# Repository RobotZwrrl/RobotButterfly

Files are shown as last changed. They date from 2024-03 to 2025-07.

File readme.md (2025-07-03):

# Robot Butterfly

[Robot Butterfly](http://robotzwrrl.xyz/robot-butterfly/) invites you to experience nature's elegance alongside it, while interacting with the surrounding wilderness! [Available now as a kit](https://robotmissions.org/store/) to build yourself. 

For more information, check out: [robotzwrrl.xyz/robot-butterfly](http://robotzwrrl.xyz/robot-butterfly/). As well, see the [instructions](https://robotzwrrl.xyz/robot-butterfly/instructions/chapter01.php) to build your own!

Robot Butterfly's design files are released as open source hardware, provided under these unique terms: If you replicate it, please take a photo of it in nature and email it to me with the city and its nickname! ☺️

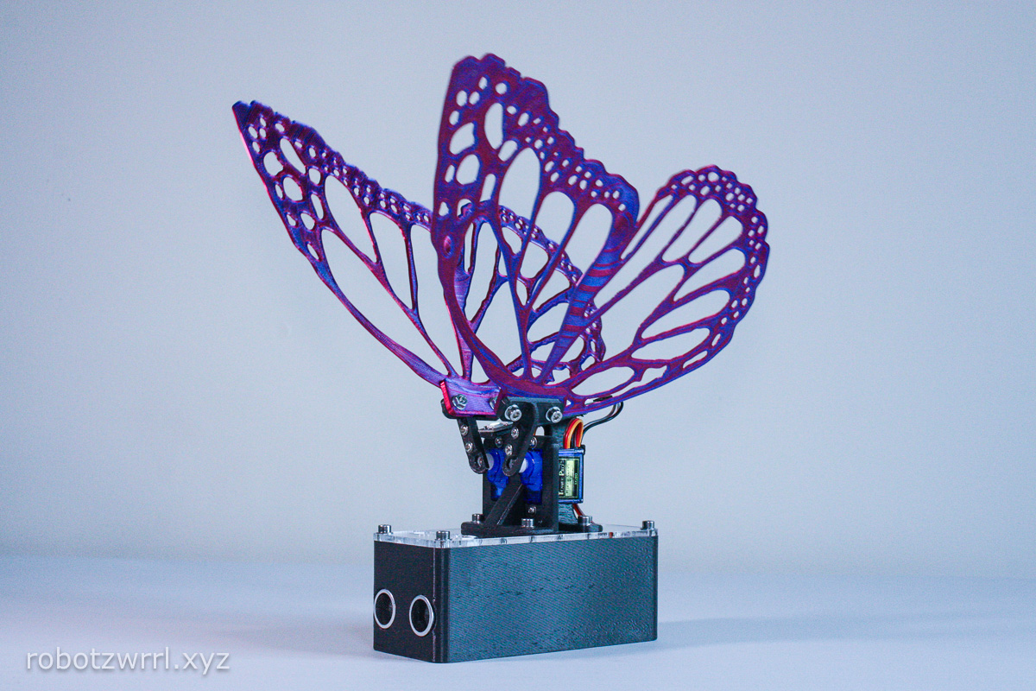
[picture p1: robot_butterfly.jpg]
Robot Butterfly


---

## Bug Fix 12-15-24

A 3D printable bugfix is available! The three pieces to print are:

- [Servo Horn Indent L](https://github.com/RobotGrrl/RobotButterfly/blob/main/3dprint/servo_horn_indent_L_v1.0.stl)
- [Servo Horn Indent R](https://github.com/RobotGrrl/RobotButterfly/blob/main/3dprint/servo_horn_indent_R_v1.0.stl)
- [Spacer Back](https://github.com/RobotGrrl/RobotButterfly/blob/main/3dprint/spacer_back_v1.1.stl)

The servo horn piece has been updated to work with the new horns that have an indent, rather than being flat in the previous version. The horn is placed on the side that has the arrow indicator. The fasteners go through holes #1 and #4. See photo below for reference.

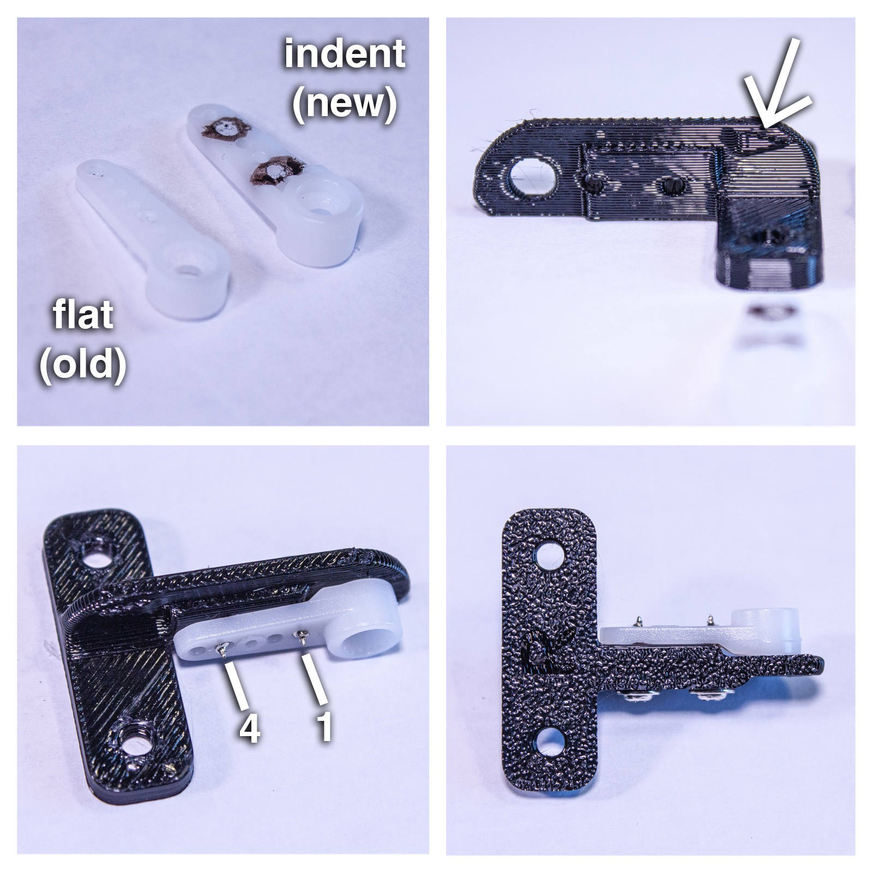
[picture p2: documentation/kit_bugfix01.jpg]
Bugfix 01


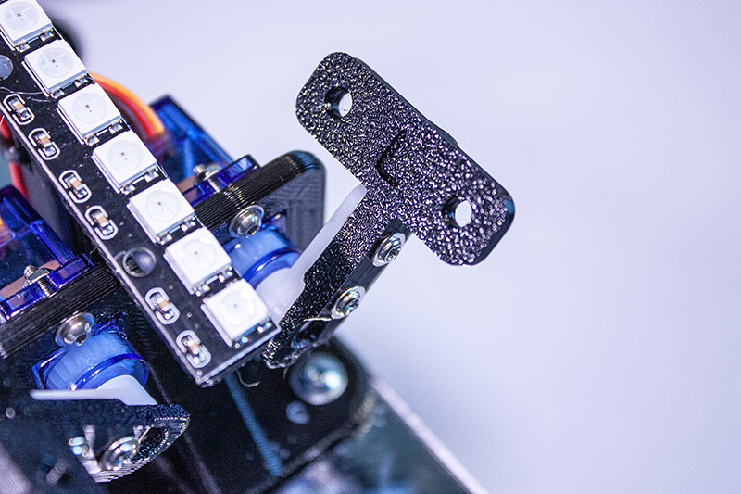
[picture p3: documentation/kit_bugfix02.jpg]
Bugfix 02


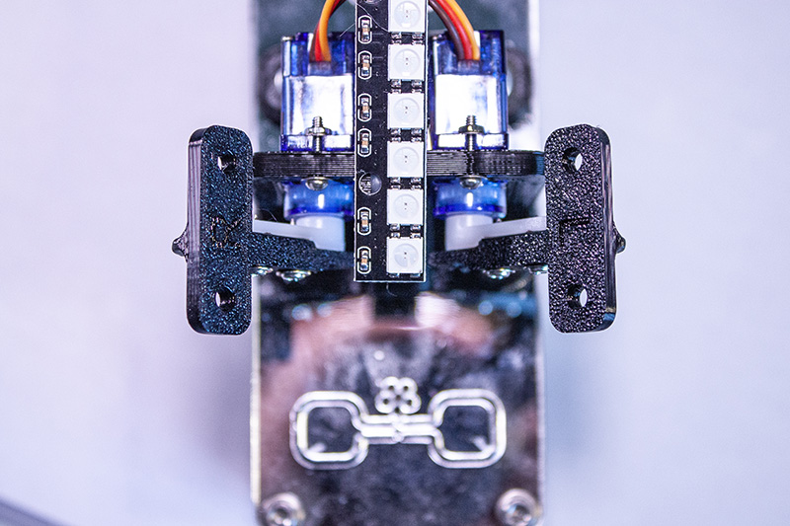
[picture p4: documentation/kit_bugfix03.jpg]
Bugfix 03


The spacer back piece has been updated to have clearance for the chamfer around the switch housing on the enclosure. This provides a cleaner fit and smoother lid installation process.

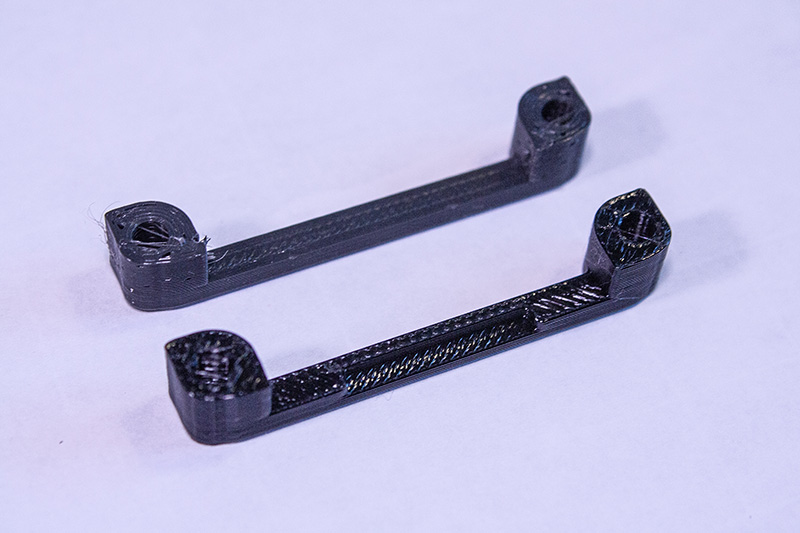
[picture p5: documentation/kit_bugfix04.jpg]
Bugfix 04


---

## Electronics

The Butterfly Chonky board connects with [Keystone](https://github.com/RobotGrrl/Keystone) and [Boostlet!](https://github.com/RobotGrrl/boostlet). Those two boards are also open source, and can be found in these repositories:

- https://github.com/RobotGrrl/boostlet
- https://github.com/RobotGrrl/Keystone

### What do the LEDs mean?

There are a few LEDs that are visible through the windows on the back of the enclosure.

On Chonky, there are two yellow 5 mm LEDs. On the left hand side, is D2. In the firmware, D2 is `LED_COMMS_PIN` (pin 5). On the right hand side, this is D1. In the firmware, D1 is `LED_HEARTBEAT_PIN` (pin 13).

LEDs from Keystone are also visible through the LED ports on the back side of the enclosure. As well, sometimes their brightness reflects in Chonky’s 5 mm LEDs. On the left hand side is power. The power LED is on all the time. On the right hand side are TX and RX. The TX and RX LEDs are activated whenever there is data on the serial port. This can be useful for a visual check, but it also just looks techno cool.

In the inaugural version, all the LEDs are yellow, which can sometimes make it tricky to visually differentiate between Chonky and Keystone's LEDs. This will be changed in a future production revision :)

---

## Manufacturing

| Piece | Layer height | Supports | Infill | Shells | Notes |
| --- | --- | --- | --- | --- | --- |
| enclosure_v1.0.stl | 0.25 mm DRAFT | Everwhere, Organic | 15% | 2 | \- |
| neopixel_bracket_v1.0.stl | 0.25 mm DRAFT | Everwhere, Organic | 15% | 3 | Prints standing up |
| battery_bracket_v1.0.stl  | 0.25 mm DRAFT | Supports to build platform | 15% | 2 | Hiya!' faces up, Top fill pattern: Octogram Spiral |
| lid_v1.1.stl | 0.25 mm DRAFT | None | 15% | 3 | Chamfer side down |
| servo_bracket_v1.0.stl | 0.25 mm DRAFT | None | 15% | 2 | Prints face down |
| servo_horn_indent_L_v1.0.stl | 0.20 mm QUALITY | None | 20% | 4 | \- |
| servo_horn_indent_R_v1.0.stl | 0.20 mm QUALITY | None | 20% | 4 | \- |
| cover_v1.0.stl | 0.25 mm DRAFT | None | 15% | 2 | Cool!' faces up |
| spacer_back_v1.1.stl | 0.25 mm DRAFT | None | 15% | 2 | Chamfer side down |
| spacer_front_v1.0.stl | 0.25 mm DRAFT | None | 15% | 2 | Chamfer side down |
| wing_L_v1.0.stl | 0.25 mm DRAFT | None | 15% | 3 | Top & bottom fill pattern: Archimedian Chords. Print 1st layer at a very slow speed. |
| wing_R_v1.0.stl | 0.25 mm DRAFT | None | 15% | 3 | Top & bottom fill pattern: Archimedian Chords. Print 1st layer at a very slow speed. |

---

## Firmware

**Firmware is in active development**

Download the [Robot Butterfly library](https://github.com/RobotZwrrl/RobotButterfly/tree/main/firmware/library/RobotButterfly) and install it into your Arduino library folder _(for example: ~/Documents/Arduino/libraries)_.

### Boards Manager

In the Arduino IDE boards manager (Tools > Board > Board Manager), search for **esp32**. Under **esp32 by Espressif Systems**, choose **2.0.4**, and install it.

### Library Dependencies

In the Arduino IDE library manager (Tools > Manage Libraries), please install the following libraries with the designated versions:

- [Streaming](https://github.com/janelia-arduino/Streaming) - v5.0.0
- [movingAvg](https://github.com/JChristensen/movingAvg) - v2.3.2
- [MPU6050](https://github.com/ElectronicCats/mpu6050) - v1.4.3
- [Adafruit Neopixel](https://github.com/adafruit/Adafruit_NeoPixel) - v.1.12.4
- [ESP32Servo](https://github.com/madhephaestus/ESP32Servo) - v3.0.6 
- [ServoEasing](https://github.com/ArminJo/ServoEasing) - v3.4.0
- [DHT](https://github.com/adafruit/DHT-sensor-library) - v1.4.6
- [Adafruit Unified Sensor](https://github.com/adafruit/Adafruit_Sensor) - v1.1.15 
- [HC-SR04](https://github.com/d03n3rfr1tz3/HC-SR04) - v1.1.3 

### Upload Code

Here's how to upload code to Robot Butterfly!

_Please see steps above to ensure all dependencies are installed properly_

1. Tools > Board > esp32 > Set board to **ESP32 Dev Module**

2. Tools > Set upload speed to **115200 baud** (at the bottom of the menu)

3. Tools > Set CPU speed to **80 MHz** (first setting after a divider in the menu)

4. Tools > Manage Libraries
There are library dependencies that will need to be downloaded, see list above

5. Open a Robot Butterfly example sketch

6. Plug in Robot Butterfly

7. Tools > Port > Select the port

8. Upload

9. Congrats! You have uploaded code to Robot Butterfly!

### Animations

For developers - here's how to make your own animation (servo and neopixel):

1. Add identifier to enum servoAnimName

`SERVO_ANIM_SOARING`

2. Add the run function prototype

`void runServoAnim_soaring(struct ServoAnimation *animation);`

3. Write the run function

`void runServoAnim_soaring(struct ServoAnimation *a) { ... }`

4. Write the init function

`void initServoAnim_soaring(struct ServoAnimation *a) { ... }`

5. Add the case to setServoAnim

`case SERVO_ANIM_SOARING: 
initServoAnim_soaring(a); 
break;`

6. Call the animation to run it!

`setServoAnim(&servo_animation_alert, SERVO_ANIM_SOARING, SERVO_ANIM_ALERT); 
startServoAnim(&servo_animation_alert);`

---

## Debugging

Please see [this page for debugging FAQ](https://robotzwrrl.xyz/robot-butterfly/instructions/debugging.php).

---

## License

Robot Butterfly (C) Copyright Erin RobotZwrrl, Robot Missions Inc.

05-30-24 v1.0

[RobotZwrrl.xyz/robot-butterfly](http://RobotZwrrl.xyz/robot-butterfly)

[RobotMissions.org](https://RobotMissions.org)

This hardware is released under:

CERN Open Hardware License Version 2.0 - Permissive (CERN-OHL-P)

[https://cern-ohl.web.cern.ch/](https://cern-ohl.web.cern.ch/)

The software is released under:

The MIT License

[https://opensource.org/license/mit](https://opensource.org/license/mit)

The documentation is released under:

CC-BY-SA-4.0

[https://creativecommons.org/licenses/by-sa/4.0/](https://creativecommons.org/licenses/by-sa/4.0/)

_Disclaimer: Distributed as is. No warranty is given. Not responsible or liable for any damage or harm that result from this product._

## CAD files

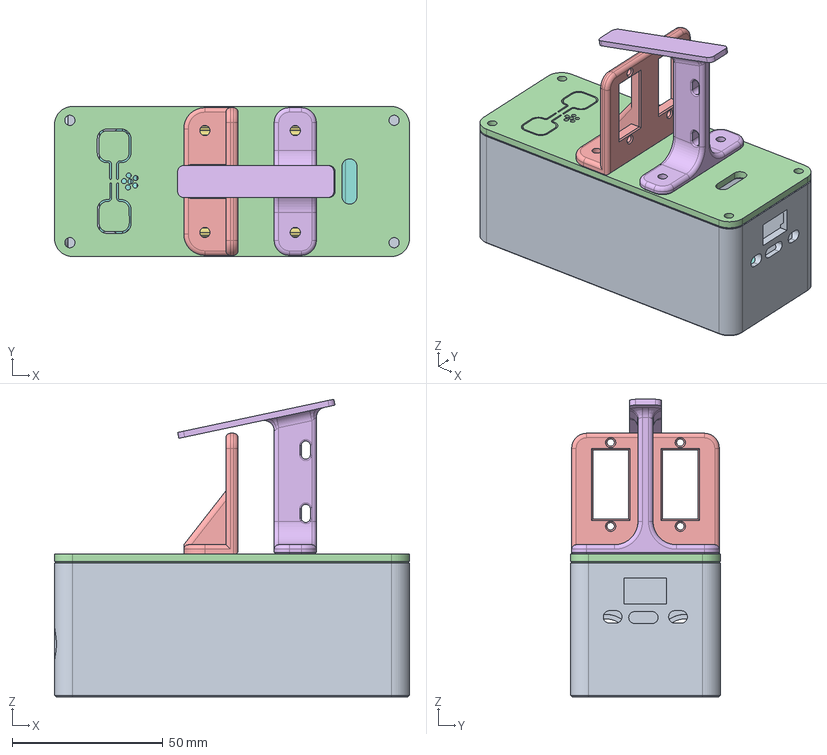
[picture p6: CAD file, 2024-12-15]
3dprint/assembly_v1.2.step
117.8 x 49.8 x 98.7 mm
enclosure_1
spacers
lid
servo bracket
neopixel bracket
cover
batt bracket

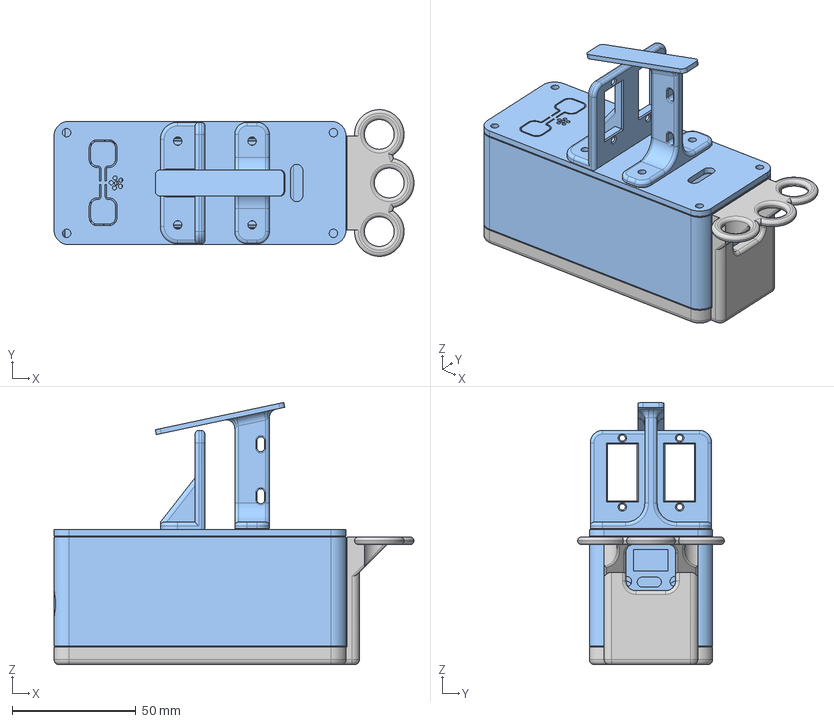
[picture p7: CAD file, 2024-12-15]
3dprint/extras/lanyard_attachment_v1.1.step
145.2 x 59.2 x 105.7 mm
enclosure_1
spacers
lid
servo bracket
neopixel bracket
cover
batt bracket

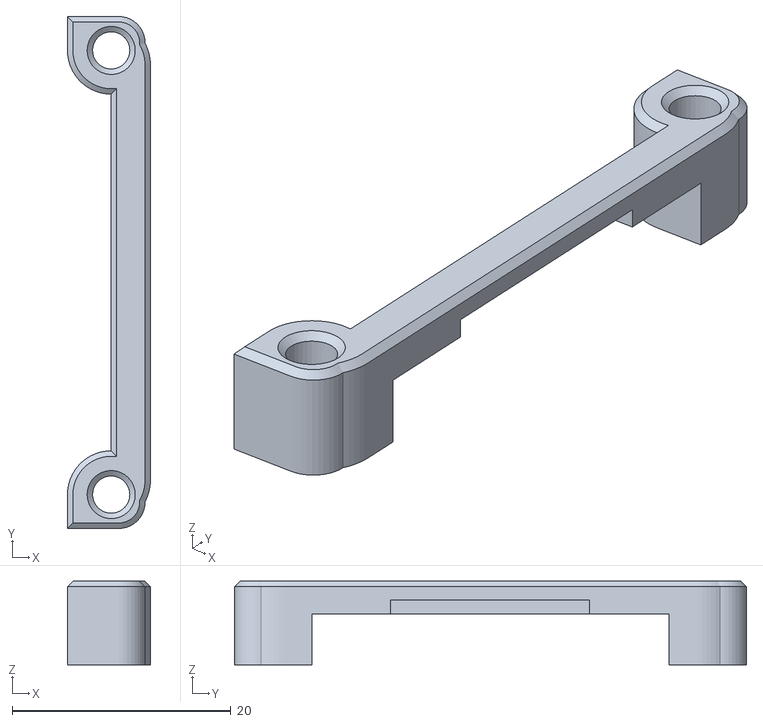
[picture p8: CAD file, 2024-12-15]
3dprint/spacer_back_v1.1.stl
7.60 x 46.8 x 7.65

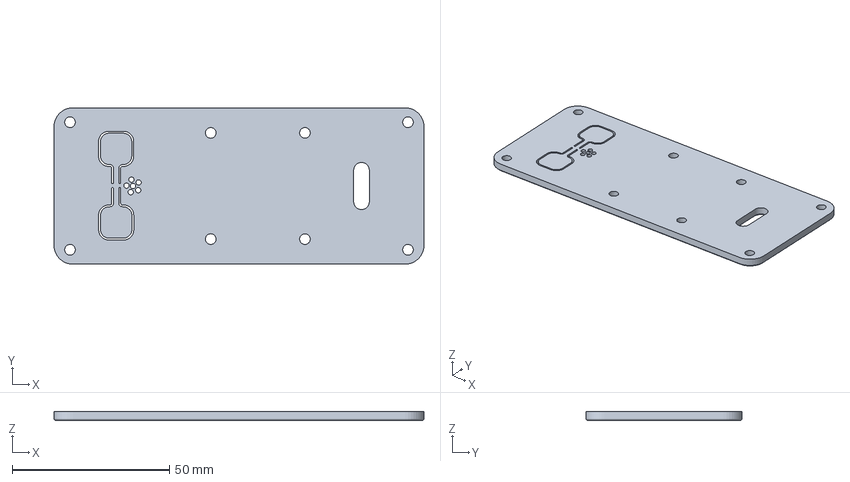
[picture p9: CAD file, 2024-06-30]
3dprint/z prusa mini/lid_v1.1.3mf
117.8 x 49.8 x 3.00 mm

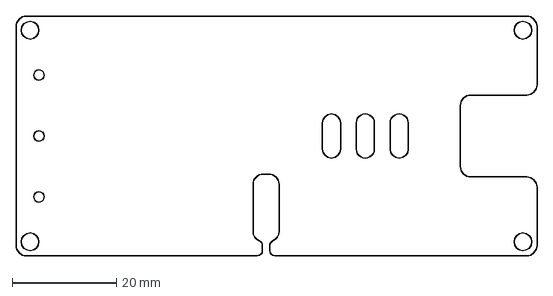
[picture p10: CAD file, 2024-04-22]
electronics/butterfly-chonky/outline-guide.dxf
100.0 x 46.0 mm

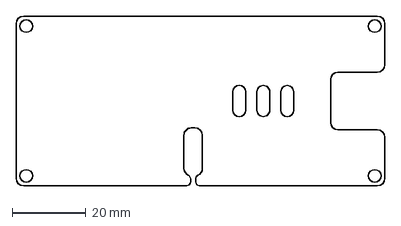
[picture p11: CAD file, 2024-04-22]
electronics/butterfly-chonky/outline.dxf
100.0 x 46.0 mm

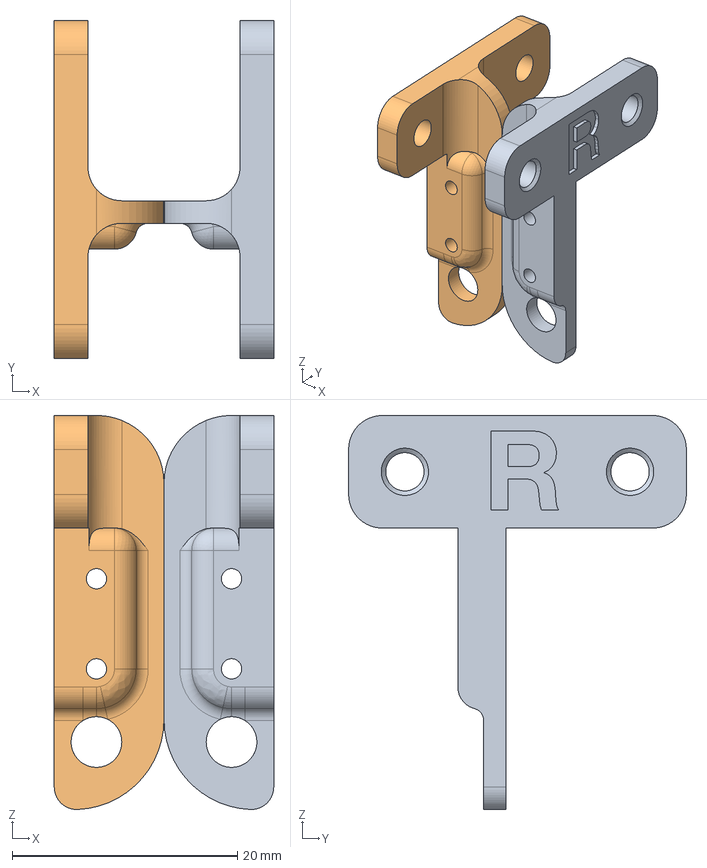
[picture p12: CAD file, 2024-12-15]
3dprint/servo_horn_flat_v1.0.step
19.5 x 30.0 x 35.0 mm
Component1(Mirror)

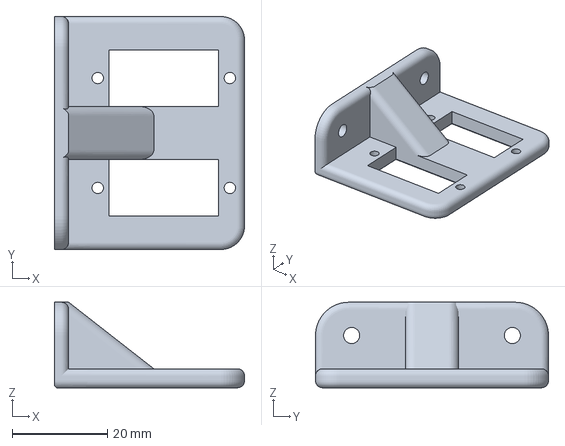
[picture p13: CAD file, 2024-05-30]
3dprint/z prusa mini/servo_bracket_v1.0.3mf
40.0 x 49.0 x 18.0 mm

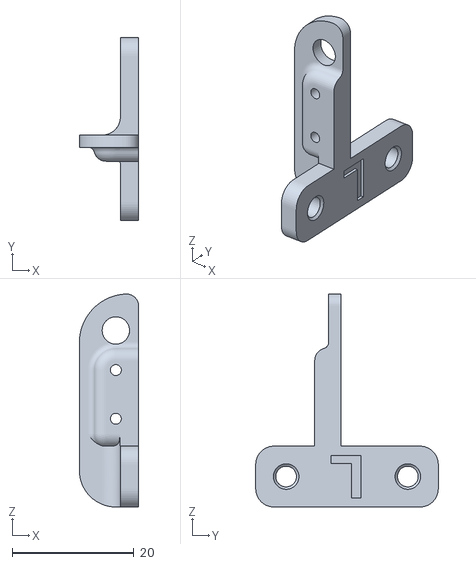
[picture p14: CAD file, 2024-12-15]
3dprint/servo_horn_flat_L_v1.0.stl
9.75 x 30.0 x 35.0

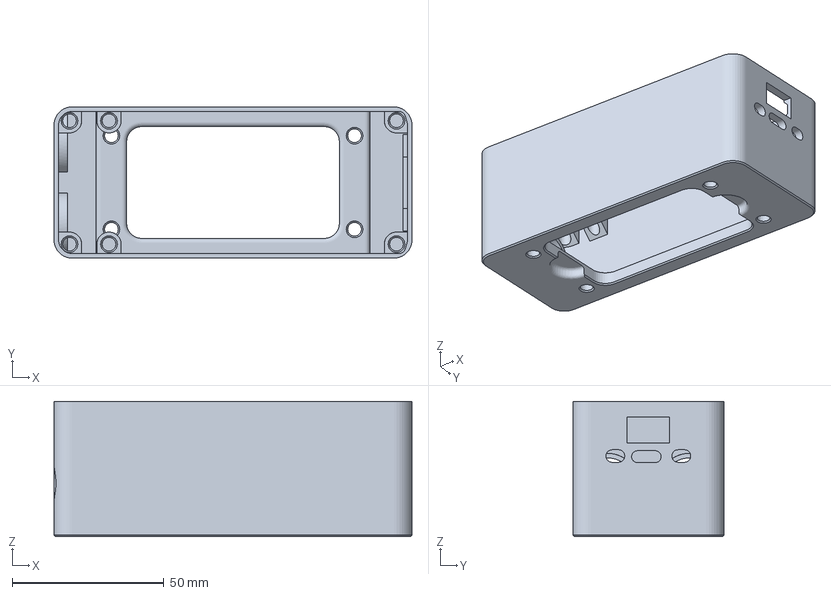
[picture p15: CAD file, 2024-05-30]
3dprint/z prusa mini/enclosure_v1.0.3mf
117.8 x 49.8 x 44.4 mm

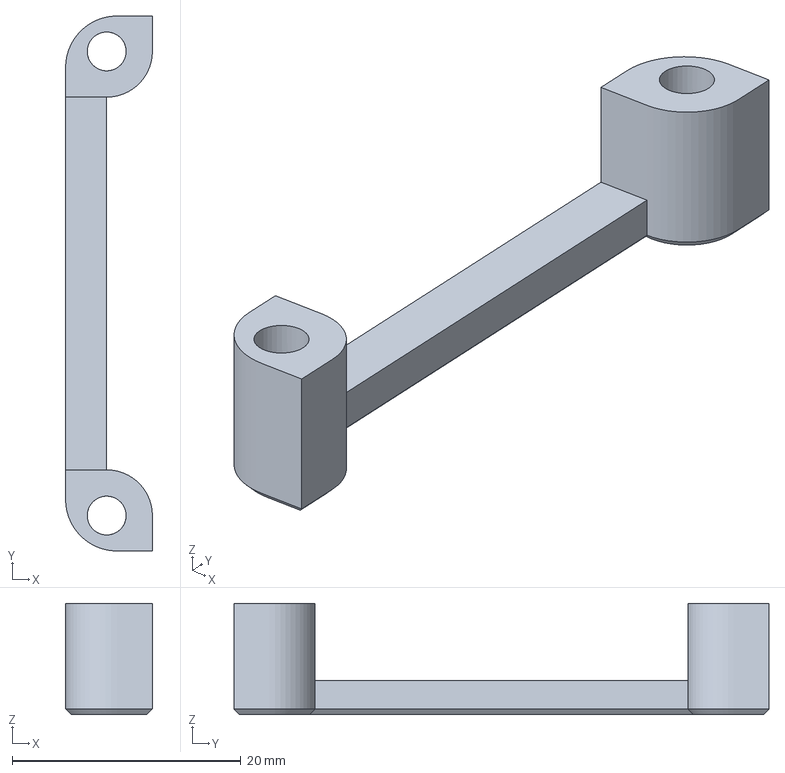
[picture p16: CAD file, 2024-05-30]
3dprint/z prusa mini/spacer_front_v1.0.3mf
7.60 x 46.8 x 9.75 mm

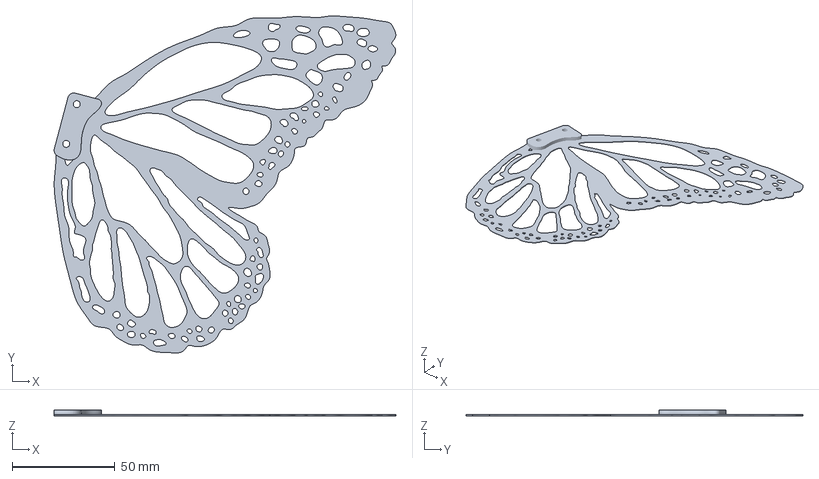
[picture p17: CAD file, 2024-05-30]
3dprint/z prusa mini/wing_L_v1.0.3mf
166.3 x 164.0 x 3.00 mm

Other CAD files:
3dprint/z prusa mini/spacer_back_v1.0.3mf
3dprint/servo_horn_indent_L_v1.0.stl
3dprint/z prusa mini/servo_horn_L_v1.0.3mf
3dprint/servo_horn_indent_v1.0.step
3dprint/servo_horn_indent_R_v1.0.stl
3dprint/servo_horn_flat_R_v1.0.stl
3dprint/archive/assembly_v1.0.step
3dprint/archive/assembly_v1.1.step
3dprint/archive/assembly_v1.1_no_colour.step
3dprint/archive/lid_v1.0.stl
3dprint/assembly_v1.1.step
3dprint/battery_bracket_v1.0.stl
3dprint/cover_v1.0.stl
3dprint/enclosure_v1.0.stl
3dprint/extras/lanyard_attachment_v1.0.step
3dprint/extras/lanyard_attachment_v1.1.stl
3dprint/lid_v1.0.dxf
3dprint/lid_v1.1.stl
3dprint/neopixel_bracket_v1.0.stl
3dprint/servo_bracket_v1.0.stl
3dprint/servo_horn_flat_v1.0.f3d
3dprint/servo_horn_indent_v1.0.f3d
3dprint/spacer_front_v1.0.stl
3dprint/wing_L_v1.0.stl
3dprint/wing_R_v1.0.stl
3dprint/z prusa mini/archive/lid_v1.0.3mf
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

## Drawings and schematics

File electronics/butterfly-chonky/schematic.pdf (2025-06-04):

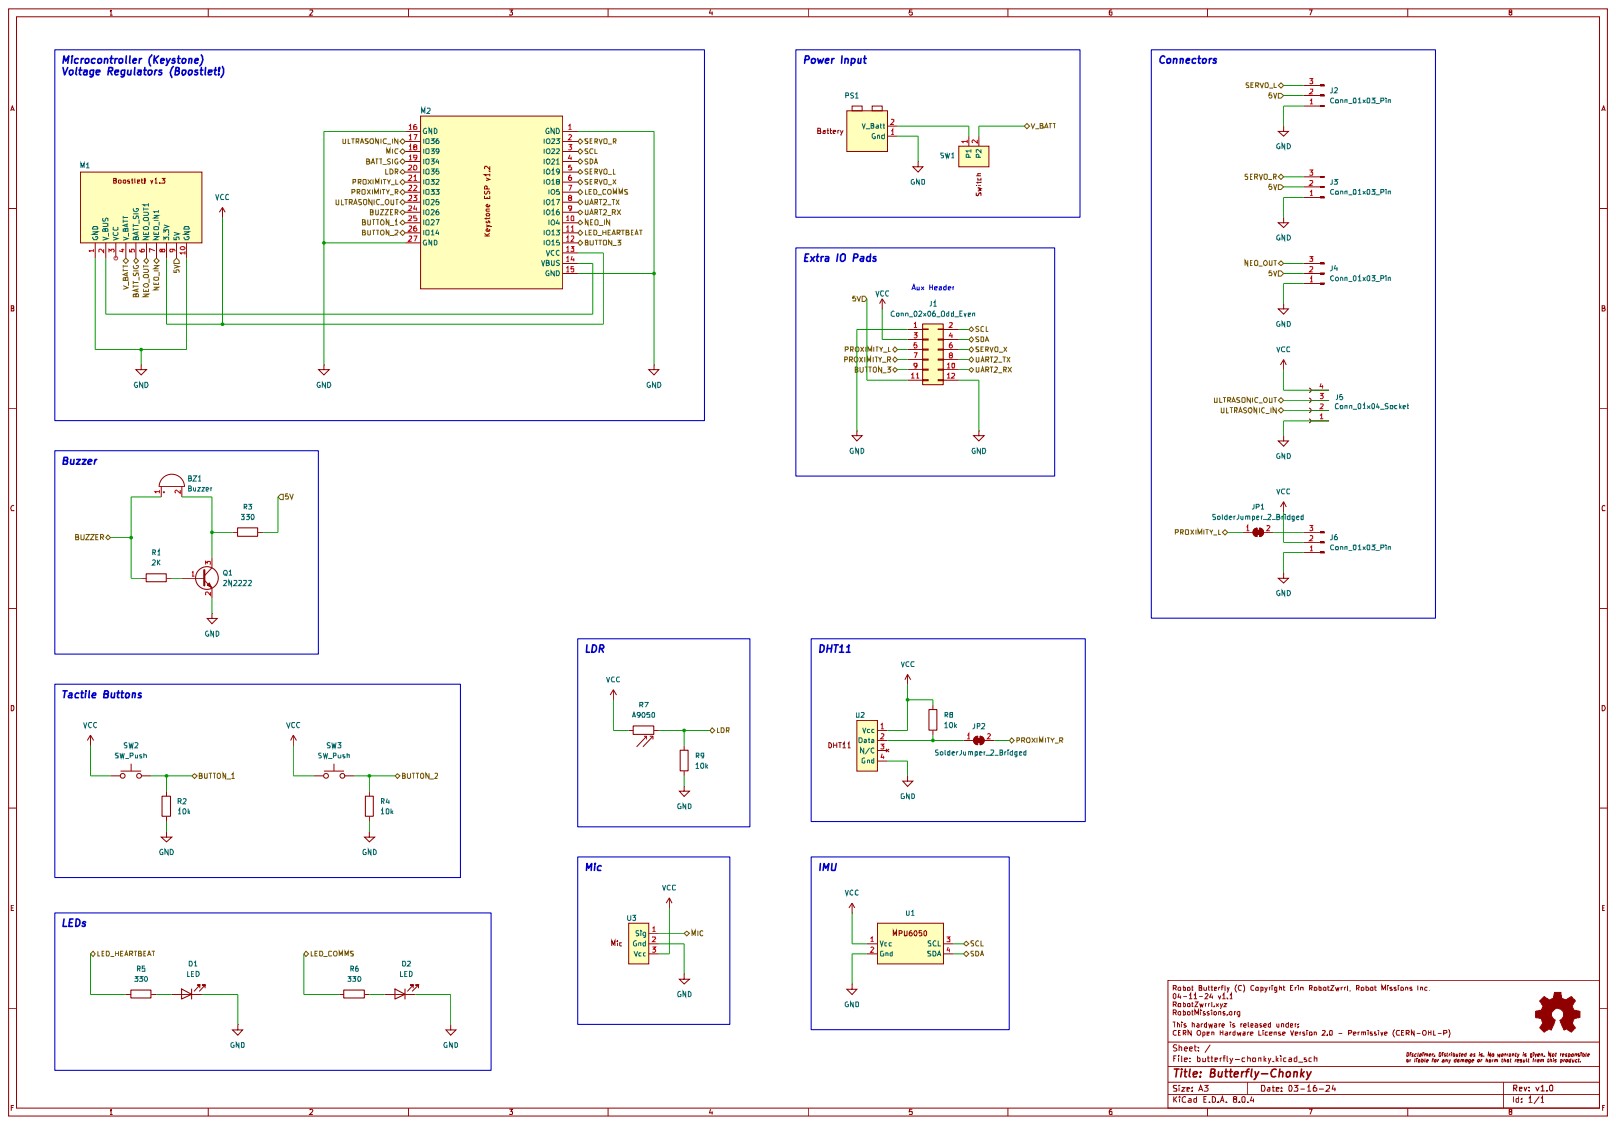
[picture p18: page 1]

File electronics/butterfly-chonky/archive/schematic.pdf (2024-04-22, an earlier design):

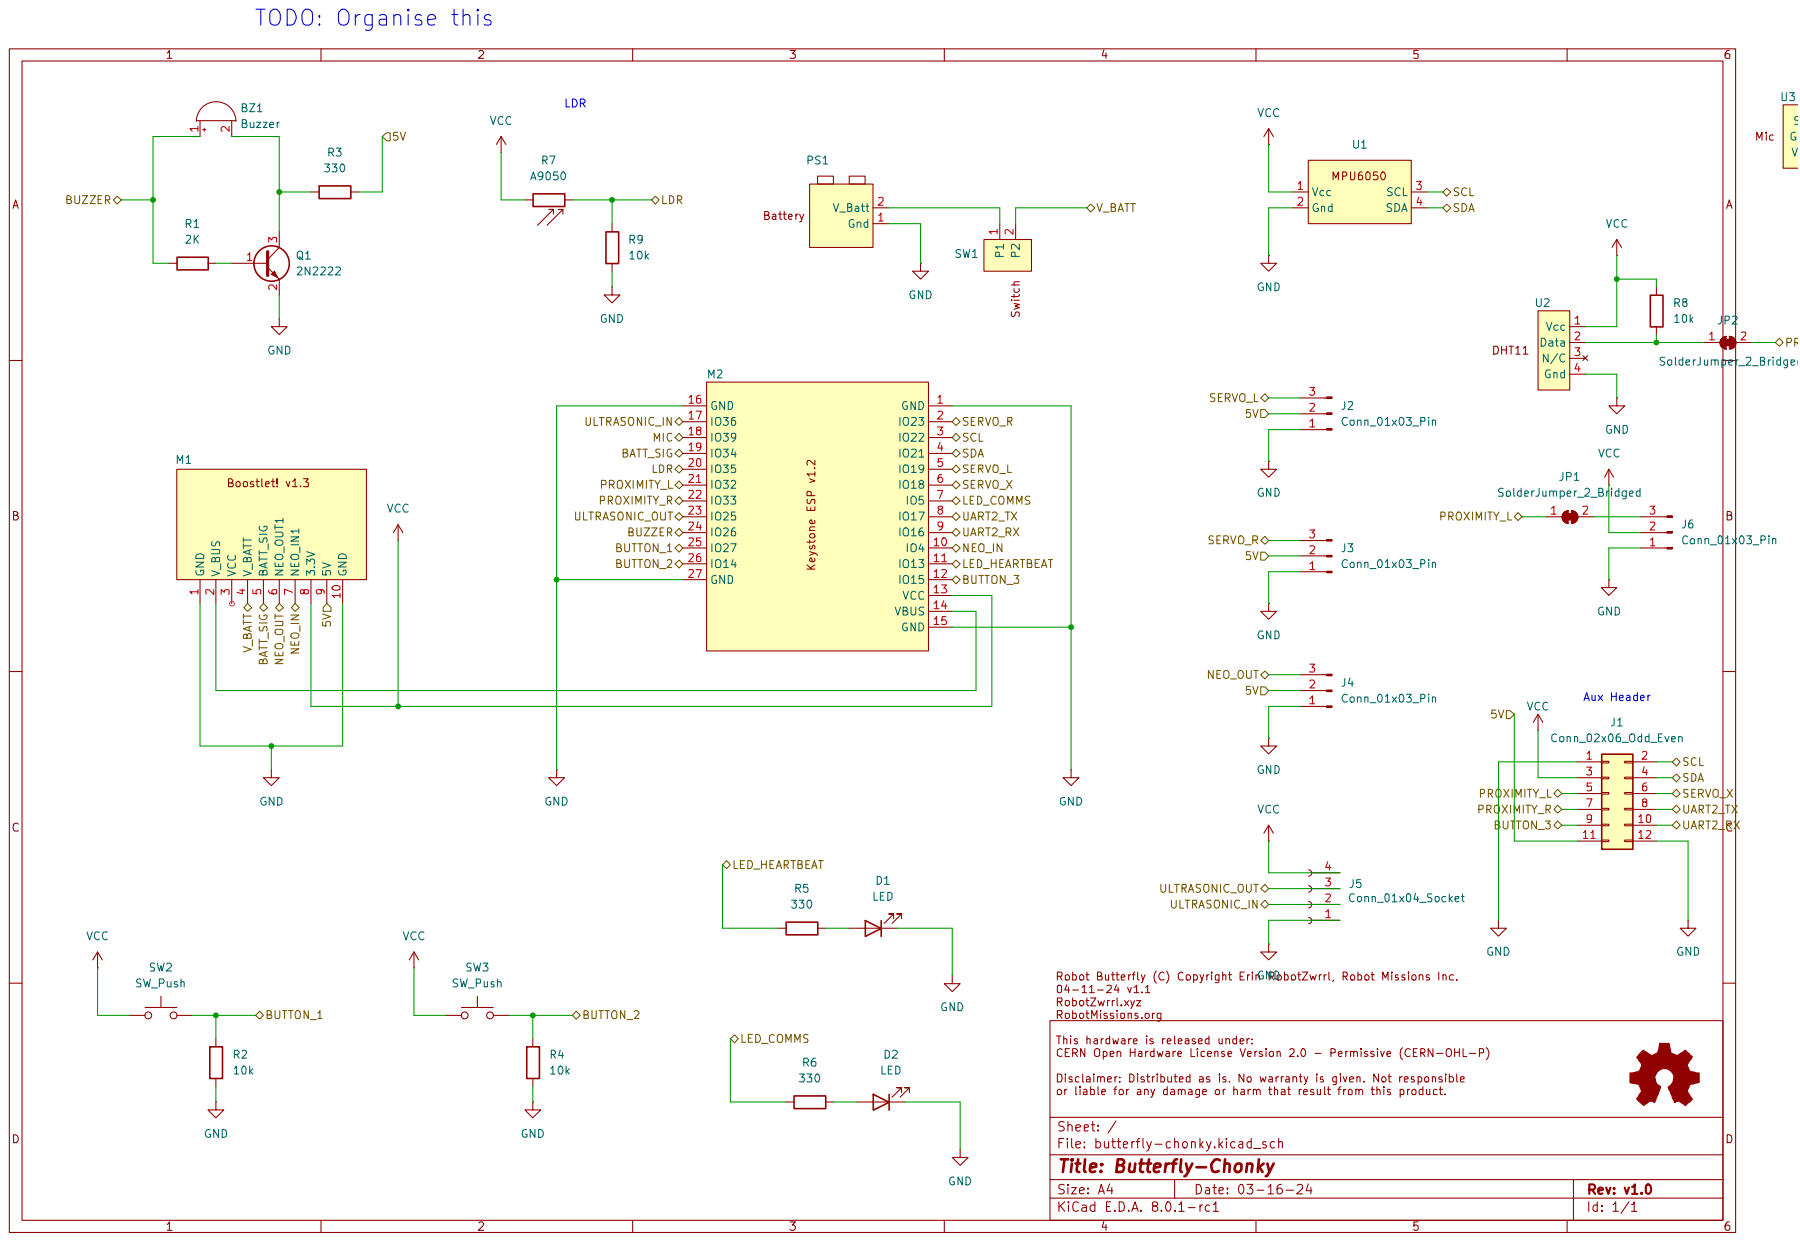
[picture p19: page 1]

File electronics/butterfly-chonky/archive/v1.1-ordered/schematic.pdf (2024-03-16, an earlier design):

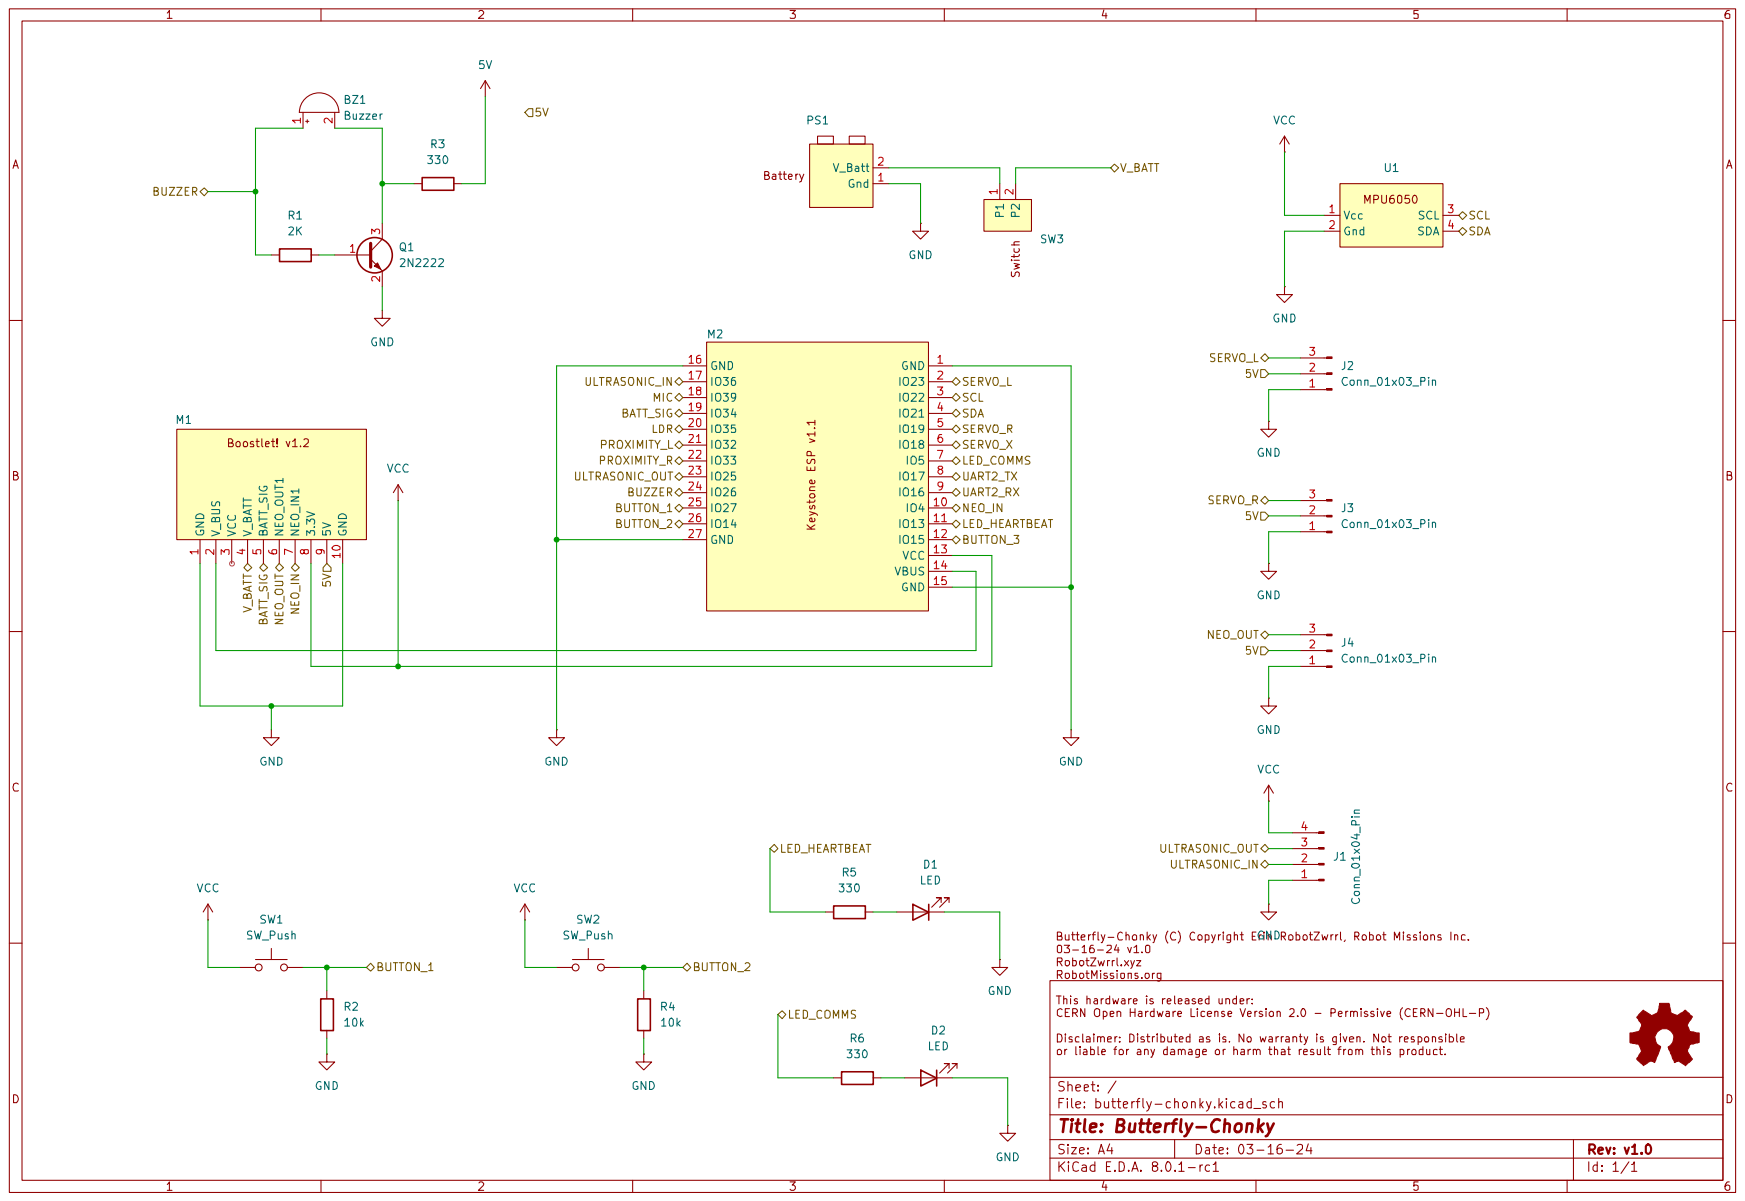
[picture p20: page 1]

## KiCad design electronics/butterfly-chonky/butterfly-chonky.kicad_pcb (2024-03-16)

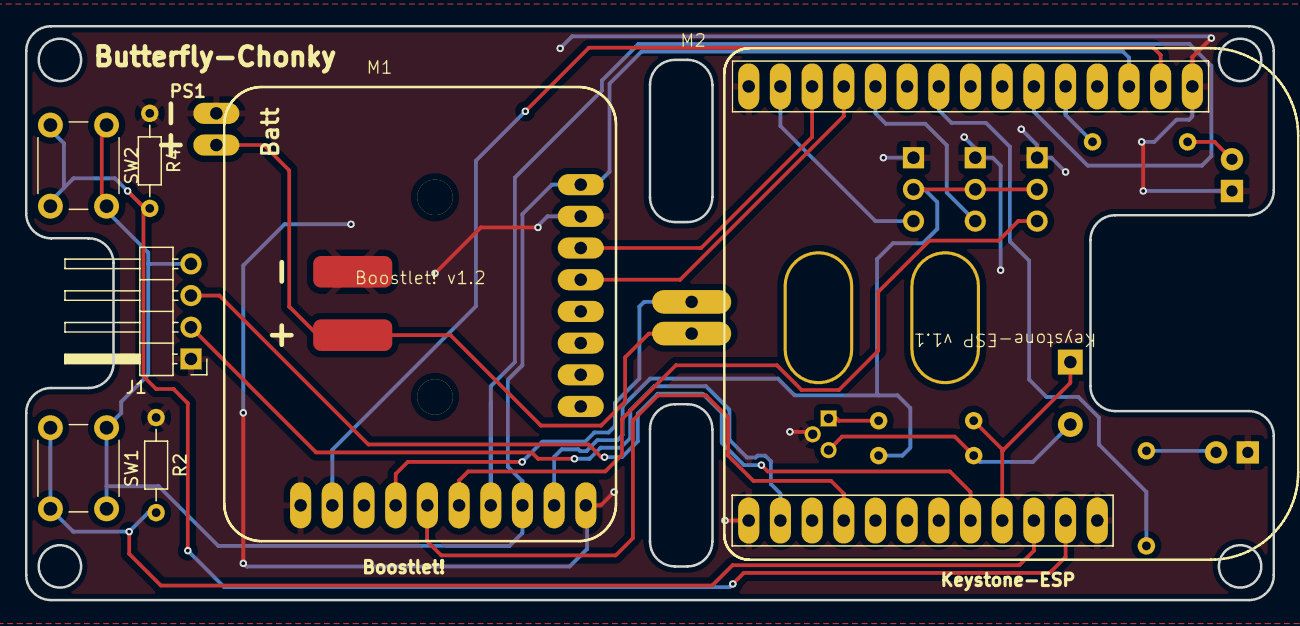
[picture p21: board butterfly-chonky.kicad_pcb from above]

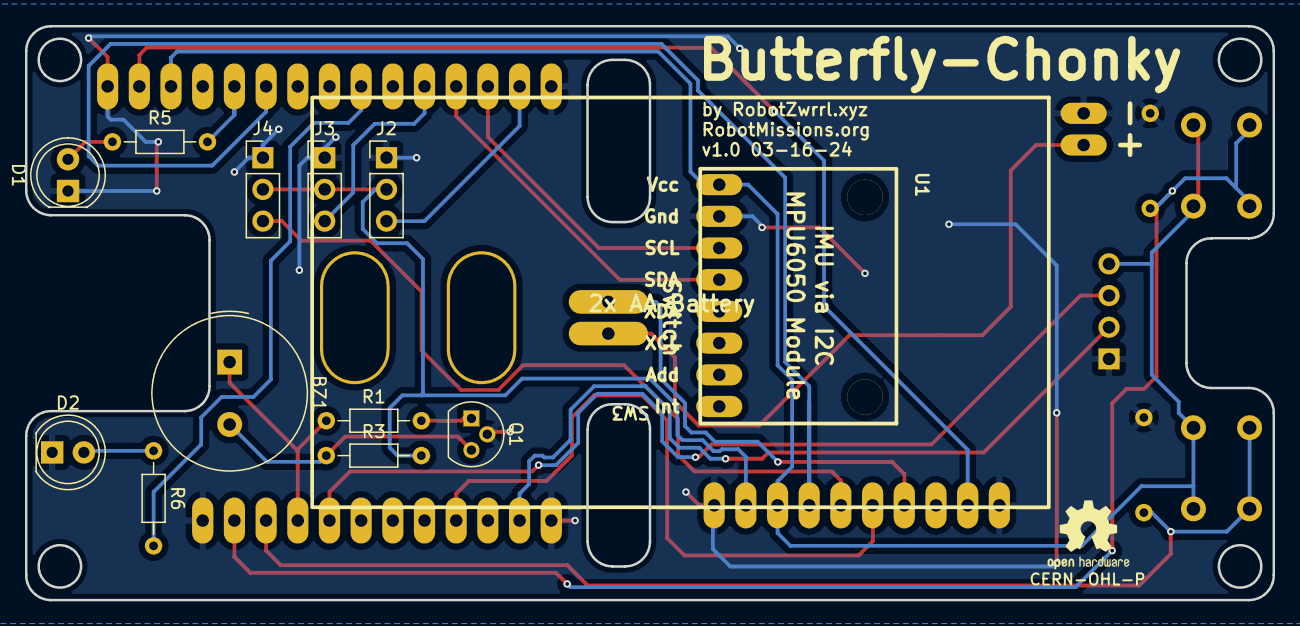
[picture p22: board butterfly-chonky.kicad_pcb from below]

Board: 2 copper layers, 100.0 x 46.0 mm, 21 parts (13 on the bottom side), 24 nets.

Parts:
BZ1: Buzzer; Buzzer_TDK_PS1240P02BT_D12.2mm_H6.5mm
D1, D2: LED; LED_D5.0mm_Clear
J1: Conn_01x04_Pin; PinHeader_1x04_P2.54mm_Horizontal
J2, J3, J4: Conn_01x03_Pin; PinHeader_1x03_P2.54mm_Vertical
M1: Boostlet_v1.2
M2: Keystone-ESP_v1.1
PS1: 2xAA_Battery_Module
Q1: 2N2222; TO-92
R1: 2K; R_Axial_DIN0204_L3.6mm_D1.6mm_P7.62mm_Horizontal
R2, R4: 10k; R_Axial_DIN0204_L3.6mm_D1.6mm_P7.62mm_Horizontal
R3, R5, R6: 330; R_Axial_DIN0204_L3.6mm_D1.6mm_P7.62mm_Horizontal
SW1, SW2: SW_Push; SW_PUSH_6mm_H5mm
SW3: Switch_Header
U1: MPU6050_Module

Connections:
5V: J2.2, J3.2, J4.2, M1.9 (5V), R3.2
/BATT_SIG: M1.5 (BATT_SIG), M2.19 (IO34)
/BUTTON_1: M2.25 (IO27), R2.2, SW1.2
/BUTTON_2: M2.26 (IO14), R4.2, SW2.2
/BUZZER: BZ1.1 (+), M2.24 (IO26), R1.1
/LED_COMMS: M2.7 (IO5), R6.2
/LED_HEARTBEAT: M2.11 (IO13), R5.2
/NEO_IN: M1.7 (NEO_IN1), M2.10 (IO4)
/NEO_OUT: J4.3, M1.6 (NEO_OUT1)
/SCL: M2.3 (IO22), U1.3 (SCL)
/SDA: M2.4 (IO21), U1.4 (SDA)
/SERVO_L: J2.3, M2.2 (IO23)
/SERVO_R: J3.3, M2.5 (IO19)
/ULTRASONIC_IN: J1.2, M2.17 (IO36)
/ULTRASONIC_OUT: J1.3, M2.23 (IO25)
/V_BATT: M1.4 (V_BATT), SW3.2
GND: D1.1 (K), D2.1 (K), J1.1, J2.1, J3.1, J4.1, M1.1 (GND), M1.10 (GND), M2.1 (GND), M2.15 (GND), M2.16 (GND), M2.27 (GND), PS1.1 (Gnd), Q1.2 (E), R2.1, R4.1, U1.2 (Gnd)
unnamed: BZ1.2 (-), Q1.3 (C), R3.1
unnamed: D1.2 (A), R5.1
unnamed: D2.2 (A), R6.1
unnamed: M1.2 (V_BUS), M2.14 (VBUS)
unnamed: PS1.2 (V_Batt), SW3.1
unnamed: Q1.1 (B), R1.2
VCC: J1.4, M1.8 (3.3V), M2.13 (VCC), SW1.1, SW2.1, U1.1 (Vcc)

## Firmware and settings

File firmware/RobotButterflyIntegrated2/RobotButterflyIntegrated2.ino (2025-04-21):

/*
 * Robot Butterfly Integrated 2
 * ----------------------------
 * Sandbox sketches together as one sketch
 * 
 * Board: ESP32 Dev Module
 * CPU speed: 80 MHz
 * Upload speed: 115200 baud
 * esp boards package: v 2.0.4 (<-- newer available)
 *
 * 21 Apr 2025 - Erin RobotZwrrl for Robot Missions Inc
 * http://robotzwrrl.xyz/robot-butterfly
 * http://robotmissions.org
 */

#include "Board.h"
#include "StateMachine_Params.h"
#include "Sound_Params.h"
#include "ServoAnim_Params.h"
#include "IMU_Params.h"
#include "Buttons_Params.h"
#include "Sensor_Params.h"
#include "Proximity_Params.h"
#include "NeoAnimations_Params.h"
#include "pitches.h"
#include <Streaming.h>
#include <ESP32Servo.h>      // 3.0.6 https://github.com/madhephaestus/ESP32Servo 
#include "ServoEasing.hpp"   // 3.4.0 https://github.com/ArminJo/ServoEasing
#include <movingAvg.h>   // 2.3.2 https://github.com/JChristensen/movingAvg
#include "DHT.h"         // 1.4.6 https://github.com/adafruit/DHT-sensor-library & 1.1.15 https://github.com/adafruit/Adafruit_Sensor 
#include <HCSR04.h>      // 1.1.3 https://github.com/d03n3rfr1tz3/HC-SR04 
#include "MPU6050.h"    // https://github.com/ElectronicCats/mpu6050/ 
#include <Adafruit_NeoPixel.h>


// ------------ states -----------
// this is where you can order the behaviours
enum StatesMachine {
  STATE1,
  STATE2,
  STATE3,
  STATE4,
  STATE5,
  STATE6,
  STATE7,
  STATE8
};

uint8_t CURRENT_STATE;
uint8_t PREV_STATE;
long last_state_change = 0;
long last_state_print = 0;

volatile bool enter_state = false;
volatile bool update_state = false;
volatile bool new_print = false;
volatile bool new_enter = false;
volatile bool new_update = false;
long t_transition = 0;
long t_enter = 0;
long t_delta = 0;

hw_timer_t *timer_state_cfg = NULL;

void IRAM_ATTR Timer_State_ISR() {
  enter_state = false;
  update_state = true;
  new_print = true;
  new_update = true;
}
// -------------------------------

// ----------- buzzer api ------------
void playSound(uint8_t id);
void soundDoneCallback(uint8_t id);
// -----------------------------------


// ------------ sound id -------------
enum soundID {
  SOUND_ALERT_STARTUP,
  SOUND_ALERT_ALERT,
  SOUND_ALERT_SLEEP,
  SOUND_ALERT_SNEEZE,
  SOUND_ALERT_MISSION_COMPLETE,
  SOUND_ALERT_MOONLIGHT_MODE,
  SOUND_ALERT_CHIRPY,
  SOUND_ALERT_WIFI_CONNECT,
  SOUND_ALERT_WIFI_DISCONNECT,
  SOUND_ALERT_MQTT_SEND,
  SOUND_ALERT_MQTT_RECEIVE,

  SOUND_SMELL_FLOWER,
  SOUND_SMELL_ROSE,
  SOUND_SMELL_WILDFLOWER,
  SOUND_SMELL_LAVENDER,
  SOUND_SMELL_DAISY,
  SOUND_SMELL_SUNFLOWER,

  SOUND_FLUTTER_MEMORY,
  SOUND_FLUTTER_JOY,
  SOUND_FLUTTER_CALM,
  SOUND_FLUTTER_SURPRISE,
  SOUND_FLUTTER_CONFUSED,
  SOUND_FLUTTER_SLEEPY,
  SOUND_FLUTTER_GRATEFUL
};
// -----------------------------------

// ----------- servo motors -----------
ServoEasing s1;
ServoEasing s2;

struct ServoMotor {
  ServoEasing motor;
  uint16_t home_pos;
  uint16_t up_pos;
  uint16_t down_pos;
  uint16_t current_pos;
  uint16_t target_pos;
  bool active;
  bool calibrated;
  String name;
};

enum ServoModeInit {
  SERVO_MODE_INIT_BOTH,
  SERVO_MODE_INIT_LEFT,
  SERVO_MODE_INIT_RIGHT
};

struct ServoMotor wing_left;
struct ServoMotor wing_right;

bool initialised_servos = false;
// -----------------------------------


// ----------- servo animation -----------
enum servoAnimName {
  SERVO_ANIM_NONE,
  SERVO_ANIM_GENTLE,
  SERVO_ANIM_SWAY,
  SERVO_ANIM_SOARING,
  SERVO_ANIM_TOUCHGRASS,
  SERVO_ANIM_SWOOSH,
  SERVO_ANIM_PARTY,
  SERVO_ANIM_FLUTTER,
  SERVO_ANIM_RANGE,
  SERVO_ANIM_POSITION
};

enum servoAnimType {
  SERVO_ANIM_ALERT,
  SERVO_ANIM_HOME
};

enum servoAnimFlutterWings {
  SERVO_ANIM_FLUTTER_WINGS_BOTH_HOME,
  SERVO_ANIM_FLUTTER_WINGS_BOTH_UP,
  SERVO_ANIM_FLUTTER_WINGS_LEFT_HOME,
  SERVO_ANIM_FLUTTER_WINGS_LEFT_UP,
  SERVO_ANIM_FLUTTER_WINGS_RIGHT_HOME,
  SERVO_ANIM_FLUTTER_WINGS_RIGHT_UP
};

enum servoAnimFlutterPos {
  SERVO_ANIM_FLUTTER_POS_NONE,
  SERVO_ANIM_FLUTTER_POS_HOME,
  SERVO_ANIM_FLUTTER_POS_UP,
  SERVO_ANIM_FLUTTER_POS_DOWN
};

enum servoAnimRangeSpan {
  SERVO_ANIM_RANGE_DOWN_UP,
  SERVO_ANIM_RANGE_HOME_UP,
  SERVO_ANIM_RANGE_ALT_HOME_UP
};

enum servoAnimPosition {
  SERVO_ANIM_POSITION_DOWN,
  SERVO_ANIM_POSITION_HOME,
  SERVO_ANIM_POSITION_UP
};

void runServoAnim_none(struct ServoAnimation *animation);
void runServoAnim_gentle(struct ServoAnimation *animation);
void runServoAnim_sway(struct ServoAnimation *animation);
void runServoAnim_soaring(struct ServoAnimation *animation);
void runServoAnim_touchgrass(struct ServoAnimation *animation);
void runServoAnim_swoosh(struct ServoAnimation *animation);
void runServoAnim_party(struct ServoAnimation *animation);
void runServoAnim_flutter(struct ServoAnimation *animation);
void runServoAnim_range(struct ServoAnimation *animation);
void runServoAnim_position(struct ServoAnimation *animation);
typedef void (*ServoAnimationFunction)(ServoAnimation*); // function pointer type that accepts a ServoAnimation pointer

struct ServoAnimation {
  uint8_t id;
  bool active;
  uint8_t type;
  uint8_t velocity;   // degrees per second

  uint8_t num_frames;
  uint16_t frame_delay;
  int frame_index;
  long last_frame;
  
  int num_repeats;
  uint16_t repeat_count;
  uint16_t repeat_delay;
  long last_repeat;

  long duration;
  long start_time;

  bool dir;
  int helper1;
  int helper2;
  int helper3;

  ServoAnimationFunction function;  // function pointer
};

ServoAnimation servo_animation_home;
ServoAnimation servo_animation_alert;
// -----------------------------------

// ------------ callbacks ------------
void proximityTriggerCallback(struct Proximity *p);
// ------------------------------------

// ----------- ultrasonic -------------
struct Proximity {
  bool initialised;
  long last_print;
  long last_trigger;
  uint8_t threshold;

  volatile bool update_raw;
  volatile uint8_t iteration_raw;
  volatile uint8_t reload_raw;
  uint16_t raw;
  uint16_t raw_prev;
  long last_raw;

  uint16_t val;
  uint16_t val_prev;
  movingAvg val_avg;

  Proximity() 
  : initialised(false), last_print(0), last_trigger(0), threshold(0),
    update_raw(false), iteration_raw(0), reload_raw(0), raw(0), raw_prev(0), last_raw(0),
    val_avg(PROXIMITY_MOVING_AVG_WINDOW, true)
{}

};

static struct Proximity ultrasonic;
// ------------------------------------

// ------------ callbacks ------------
void sensorLightChangeCallback(struct Sensor *s, bool trigger_dir);
void sensorLightAmbientChangeCallback(struct Sensor *s, int change);
void sensorSoundChangeCallback(struct Sensor *s, bool trigger_dir);
void sensorSoundAmbientChangeCallback(struct Sensor *s, int change);
void sensorTemperatureChangeCallback(struct Sensor *s, bool trigger_dir);
void sensorTemperatureAmbientChangeCallback(struct Sensor *s, int change);
void sensorHumidityChangeCallback(struct Sensor *s, bool trigger_dir);
void sensorHumidityAmbientChangeCallback(struct Sensor *s, int change);
// ------------------------------------

// -------------- vars ---------------
DHT dht(DHT11_PIN, DHT11);

uint16_t getSensor_Light(struct Sensor *s);
void updateSensor_Light(struct Sensor *s);
uint16_t getSensor_Battery(struct Sensor *s);
void updateSensor_Battery(struct Sensor *s);
uint16_t getSensor_Sound(struct Sensor *s);
void updateSensor_Sound(struct Sensor *s);
uint16_t getSensor_Temperature(struct Sensor *s);
void updateSensor_Temperature(struct Sensor *s);
uint16_t getSensor_Humidity(struct Sensor *s);
void updateSensor_Humidity(struct Sensor *s);
typedef uint16_t (*SensorDAQFunction)(Sensor*); // function pointer type that accepts a Sensor pointer
typedef void (*SensorUpdateFunction)(Sensor*); // function pointer type that accepts a Sensor pointer
// ------------------------------------

// --------------- sensor ----------------
hw_timer_t *timer_10Hz_config = NULL;

enum SensorIDs {
  SENSOR_ID_LIGHT,  
  SENSOR_ID_BATTERY,
  SENSOR_ID_SOUND,
  SENSOR_ID_TEMPERATURE,
  SENSOR_ID_HUMIDITY
};

struct Sensor {
  uint8_t id;
  String name;
  bool print;
  long print_frequency;
  long last_print;
  uint16_t trig_count;
  bool trigger_dir;
  long last_sensor_trigger;
  long last_ambient_trigger;

  // collected every 0.1 seconds
  volatile bool update_raw;
  volatile uint8_t iteration_raw;
  volatile uint8_t reload_raw;
  uint16_t raw;
  uint16_t raw_prev;
  long last_raw;

  // averaged over 1 seconds
  volatile bool update_val;
  volatile uint8_t iteration_val;
  volatile uint8_t reload_val;
  uint16_t val;
  uint16_t val_prev;
  long last_val;
  movingAvg val_avg;

  // averaged over 60 seconds
  volatile bool update_ambient;
  volatile uint16_t iteration_ambient;
  volatile uint16_t reload_ambient;
  uint16_t ambient;
  uint16_t ambient_prev;
  long last_ambient;
  movingAvg ambient_avg;
  int ambient_data[6];

  // ---
  SensorDAQFunction getRawData;        // function pointer
  SensorUpdateFunction updateSensor;   // function pointer

  // constructor
  Sensor()
  : id(0), name(""), print(true), print_frequency(0), last_print(0), trig_count(0), trigger_dir(false), last_sensor_trigger(0), last_ambient_trigger(0),
    update_raw(false), iteration_raw(0), reload_raw(0), raw(0), raw_prev(0), last_raw(0),
    update_val(false), iteration_val(0), reload_val(0), val(0), val_prev(0), last_val(0),
    val_avg(SENSOR_MOVING_AVG_VAL_WINDOW, true),
    update_ambient(false), iteration_ambient(0), reload_ambient(0), ambient(0), ambient_prev(0), last_ambient(0),
    ambient_avg(SENSOR_MOVING_AVG_AMBIENT_WINDOW, true),
    ambient_data(),
    getRawData(NULL), updateSensor(NULL)
  {}

};

static struct Sensor sensor_temperature;
static struct Sensor sensor_humidity;
static struct Sensor sensor_light;
static struct Sensor sensor_sound;
static struct Sensor sensor_battery;

static struct Sensor *all_sensors[NUM_SENSORS];

static bool dht_toggle = true;
static bool dht_processed = false;
static long last_dht_processed = 0;
// ------------------------------------

// ------------- sensor isr --------------
void IRAM_ATTR Timer_10Hz_ISR() { // every 0.1 seconds

  for(uint8_t i=0; i<NUM_SENSORS; i++) {
    struct Sensor *s = all_sensors[i];
    if(s == NULL) continue;

    // update raw every 0.1 second
    if(s->iteration_raw >= s->reload_raw-1) {
      s->update_raw = true; 
      s->iteration_raw = 0;
    } else {
      if(s->update_raw == false) {
        s->iteration_raw++;
      }
    }

    // update val every 1 second
    if(s->iteration_val >= s->reload_val-1) {
      s->update_val = true;
      s->iteration_val = 0;
    } else {
      if(s->update_val == false) {
        s->iteration_val++;
      }
    }

    // update ambient every 60 seconds
    if(s->iteration_ambient >= s->reload_ambient-1) {
      s->update_ambient = true;
      s->iteration_ambient = 0;
    } else {
      if(s->update_ambient == false) {
        s->iteration_ambient++;
      }
    }

  }


  // refresh ultrasonic every 0.5 seconds
  if(ultrasonic.iteration_raw >= ultrasonic.reload_raw-1) {
    ultrasonic.update_raw = true;
    ultrasonic.iteration_raw = 0;
  } else {
    if(ultrasonic.update_raw == false) {
      ultrasonic.iteration_raw++;
    }
  }


}
// ------------------------------------

// ----------- neoanim callbacks -----------
void callback_NeoAnimDone(struct NeoAnimation *a);
void callback_NeoAnimLoop(struct NeoAnimation *a);
// -----------------------------------


// ----------- neopixel colours -----------
// go with 400 kHz as 800 kHz would leave pixel colour ghosts
Adafruit_NeoPixel pixels(NEOPIXEL_COUNT, NEOPIXEL_PIN, NEO_GRB + NEO_KHZ400);

enum pastelIndex {
  NEO_RED,
  NEO_ORANGE,
  NEO_GOLDEN_YELLOW,
  NEO_CANARY_YELLOW,
  NEO_GREEN,
  NEO_SKY_BLUE,
  NEO_BLUE,
  NEO_CYAN,
  NEO_PURPLE,
  NEO_LAVENDER,
  NEO_PINK,
  NEO_MAGENTA,
  NEO_WARM_WHITE,
  NEO_WHITE,
  NEO_OFF
};

String pastelNames[NUM_PALETTE_COLOURS] = {
  "Red",
  "Orange",
  "Golden Yellow",
  "Canary Yellow",
  "Green",
  "Sky Blue",
  "Blue",
  "Cyan",
  "Purple",
  "Lavender",
  "Pink",
  "Magenta",
  "Warm White",
  "White",
  "Off"
};

// these are the colour settings when the 
// brightness is set to 20, which is visible
// during daylight outdoors
uint16_t pastelColours[NUM_PALETTE_COLOURS][3] = {
    {  100,  180,  250},   // red
    { 3500,  190,  250},   // orange
    { 6622,  190,  250},   // golden yellow
    { 9000,  190,  250},   // canary yellow
    {15545,  170,  250},   // green
    {32845,   50,  250},   // sky blue
    {43691,  120,  250},   // blue
    {27306,  120,  250},   // cyan
    {51613,  130,  250},   // purple
    {56613,   40,  250},   // lavendar
    {  359,   90,  250},   // pink
    {63535,  140,  250},   // magenta
    { 6561,  140,  250},   // warm white
    { 8192,   90,  250},   // white
    {    0,    0,    0},   // off
};

uint32_t colourPalette[NUM_PALETTE_COLOURS];
// -----------------------------------

// ------- neopixel animation --------
enum neoAnimName {
  NEO_ANIM_NONE,
  NEO_ANIM_POLKADOT,
  NEO_ANIM_SQUIGGLE,
  NEO_ANIM_RANGE,
  NEO_ANIM_FUNKY,
  NEO_ANIM_ZWOOP,
  NEO_ANIM_SPRINKLE,
  NEO_ANIM_RAINBOW,
  NEO_ANIM_RAINBOW_ALL,
  NEO_ANIM_BOUNCE,
  NEO_ANIM_BREATHE,
  NEO_ANIM_CYCLE8,
  NEO_ANIM_CYCLE3,
  NEO_ANIM_AMBIANCE,
  NEO_ANIM_UNO
};

enum neoAnimType {
  NEO_ANIM_ALERT,
  NEO_ANIM_HOME
};

enum neoAnimAmbianceID {
  NEO_ANIM_AMBIANCE_SPRING,
  NEO_ANIM_AMBIANCE_SUMMER,
  NEO_ANIM_AMBIANCE_AUTUMN,
  NEO_ANIM_AMBIANCE_WINTER,
  NEO_ANIM_AMBIANCE_TUTTI_FRUITI
};

void runNeoAnim_none(struct NeoAnimation *animation);
void runNeoAnim_polkadot(struct NeoAnimation *animation);
void runNeoAnim_squiggle(struct NeoAnimation *animation);
void runNeoAnim_range(struct NeoAnimation *animation);
void runNeoAnim_funky(struct NeoAnimation *animation);
void runNeoAnim_zwoop(struct NeoAnimation *animation);
void runNeoAnim_sprinkle(struct NeoAnimation *animation);
void runNeoAnim_rainbow(struct NeoAnimation *animation);
void runNeoAnim_rainbow_all(struct NeoAnimation *animation);
void runNeoAnim_bounce(struct NeoAnimation *animation);
void runNeoAnim_breathe(struct NeoAnimation *animation);
void runNeoAnim_cycle8(struct NeoAnimation *animation);
void runNeoAnim_cycle3(struct NeoAnimation *animation);
void runNeoAnim_ambiance(struct NeoAnimation *animation);
void runNeoAnim_uno(struct NeoAnimation *animation);
typedef void (*AnimationFunction)(NeoAnimation*); // function pointer type that accepts a NeoAnimation pointer

struct NeoAnimation {
  uint8_t id;
  bool active;
  uint8_t type;

  uint8_t colour_primary;    // enum of the colour
  uint8_t colour_secondary;  // enum of the colour

  uint8_t num_frames;
  int frame_delay;
  uint8_t frame_index;
  long last_frame;
  
  int num_repeats;
  uint16_t repeat_count;
  uint16_t repeat_delay;
  long last_repeat;

  long duration;
  long start_time;

  bool dir;
  int helper1;
  int helper2;
  int helper3;

  AnimationFunction function;  // function pointer
};

NeoAnimation neo_animation_home;
NeoAnimation neo_animation_alert;
// -----------------------------------

// ------------ callbacks ------------
void imuStateChangeCallback(uint8_t s);
void imuOrientationChangeCallback(uint8_t o);
void imuPoseChangeCallback(uint8_t p);
void imuEventDetectedCallback(uint8_t e);
// ------------------------------------

// --------------- imu ----------------
hw_timer_t *timer_10Hz_imu_cfg = NULL;
volatile bool new_avg_sample = false;

MPU6050 mpu;

struct IMUData {
  int16_t ax, ay, az;
  int16_t gx, gy, gz;
  long last_data;
};

static struct IMUData imu;
static struct IMUData imu_prev;
static struct IMUData imu_avg;
static struct IMUData imu_home;
static struct IMUData imu_delta_home_avg;

enum IMUStates {
  IMU_SETTLE,
  IMU_CALIBRATE_HOME,
  IMU_ACTIVE,
  IMU_INACTIVE
};

uint8_t IMU_STATE = IMU_INACTIVE;
uint8_t IMU_STATE_PREV = IMU_INACTIVE;

enum IMUOrientations {
  IMU_TABLETOP,
  IMU_HANG,
  IMU_UNKNOWN
};

uint8_t IMU_ORIENTATION = IMU_UNKNOWN;
uint8_t IMU_ORIENTATION_PREV = IMU_UNKNOWN;
long last_orientation_change = 0;

enum IMUPoses {
  IMU_Pose_Tilt_L,
  IMU_Pose_Tilt_R,
  IMU_Pose_Tilt_Fwd,
  IMU_Pose_Tilt_Bwd,
  IMU_Pose_Home,
  IMU_Pose_NA
};

uint8_t IMU_POSE = IMU_Pose_NA;
uint8_t IMU_POSE_PREV = IMU_Pose_NA;
long last_pose_detected = 0;

bool EVENT_DETECTED = false;
long last_event_detected = 0;
long last_event_score_clear = 0;
int event_score = 0;

movingAvg imu_avg_data_ax(IMU_MOVING_AVG_WINDOW);
movingAvg imu_avg_data_ay(IMU_MOVING_AVG_WINDOW);
movingAvg imu_avg_data_az(IMU_MOVING_AVG_WINDOW);
movingAvg imu_avg_data_gx(IMU_MOVING_AVG_WINDOW);
movingAvg imu_avg_data_gy(IMU_MOVING_AVG_WINDOW);
movingAvg imu_avg_data_gz(IMU_MOVING_AVG_WINDOW);

movingAvg imu_avg_home_ax(IMU_MOVING_AVG_WINDOW);
movingAvg imu_avg_home_ay(IMU_MOVING_AVG_WINDOW);
movingAvg imu_avg_home_az(IMU_MOVING_AVG_WINDOW);
movingAvg imu_avg_home_gx(IMU_MOVING_AVG_WINDOW);
movingAvg imu_avg_home_gy(IMU_MOVING_AVG_WINDOW);
movingAvg imu_avg_home_gz(IMU_MOVING_AVG_WINDOW);

long last_imu_calib_print = 0;
long last_home_calibration = 0;
long settle_start = 0;
long calibration_start = 0;
long last_score_clear = 0;
int home_recalibrate_score = 0;
long last_imu_stats_print = 0;

bool IMU_PRINT_RAW = false;
bool IMU_PRINT_DATA_AVG = false;
bool IMU_PRINT_DELTA_HOME_AVG = false; // usually true during dev
bool IMU_PRINT_DELTA_TIME_AVG = false;
bool IMU_PRINT_STATS = true; // usually true during testing
// ------------------------------------

// ------------- imu isr --------------
void IRAM_ATTR Timer_10Hz_imu_ISR() { // every 0.1 seconds
  new_avg_sample = true;
}
// ------------------------------------

// ----------- buttons -----------
enum ButtonNames {
  BUTTON_LEFT,
  BUTTON_RIGHT,
  BUTTON_BOTH
};

enum ButtonStates {
  BUTTON_IDLE,
  BUTTON_RELEASED,
  BUTTON_BOTH_HOLD,
  BUTTON_HOLD,
  BUTTON_PRESSED,
  BUTTON_CLICK
};

struct Button {
  uint8_t state;
  uint8_t state_prev;
  bool pressed;
  bool flag_pressed;
  bool flag_released;
  bool flag_state_change;
  bool flag_button_hold_notif;
  long press_time;
  long release_time;
  long release_both_time;
  long click_time;
  char name;
};

static struct Button Button_L;
static struct Button Button_R;
// -----------------------------------


// -------- button callbacks ---------
void buttonHoldNotificationCallback(uint8_t n);
void buttonHoldReleasedCallback(uint8_t n);
void buttonClickCallback(uint8_t n);
void buttonReleaseCallback(uint8_t n);
// -----------------------------------

volatile bool button_L_changed = false;
volatile bool button_R_changed = false;

// ----------- buttons isr -----------
void IRAM_ATTR button_L_isr() {
  button_L_changed = true;
}

void IRAM_ATTR button_R_isr() {
  button_R_changed = true;
}
// -----------------------------------

// ------------ other ------------
long last_print = 0;
int counter = 0;
bool BATTERY_AA_MODE = true;
// -------------------------------

// ----- servo calibration -------
bool SERVO_CAL_MODE = false;
bool left_cal_dir = true;
int left_cal_mode = 0;
bool right_cal_dir = true;
int right_cal_mode = 0;
bool button_calib_changed = false;
int servo_calib_pos_left = 0;
int servo_calib_pos_right = 0;
// -------------------------------

uint8_t BUTTON1_PREV = 0;
uint8_t BUTTON2_PREV = 0;
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
void loop() {
  
  if(!SERVO_CAL_MODE) {
    updateStateMachine();
  } else {

    if(button_calib_changed) {

      if(left_cal_mode == 0) { // wing up
        servo_calib_pos_left = SERVO_ANIM_POSITION_UP;
      } else if(left_cal_mode == 1) { // wing home
        servo_calib_pos_left = SERVO_ANIM_POSITION_HOME;
      } else if(left_cal_mode == 2) { // wing down
        servo_calib_pos_left = SERVO_ANIM_POSITION_DOWN;
      }

      if(right_cal_mode == 0) { // wing up
        servo_calib_pos_right = SERVO_ANIM_POSITION_UP;
      } else if(right_cal_mode == 1) { // wing home
        servo_calib_pos_right = SERVO_ANIM_POSITION_HOME;
      } else if(right_cal_mode == 2) { // wing down
        servo_calib_pos_right = SERVO_ANIM_POSITION_DOWN;
      }

      setServoAnim(&servo_animation_alert, SERVO_ANIM_POSITION, SERVO_ANIM_ALERT);
      setServoAnimRepeats(&servo_animation_alert, -99);
      setServoAnimPositionLeft(&servo_animation_alert, servo_calib_pos_left);
      setServoAnimPositionRight(&servo_animation_alert, servo_calib_pos_right);
      startServoAnim(&servo_animation_alert);

      setNeoAnim(&neo_animation_alert, NEO_ANIM_UNO, NEO_ANIM_ALERT);
      setNeoAnimColours(&neo_animation_alert, NEO_GREEN, NEO_GREEN);
      setNeoAnimSpeed(&neo_animation_alert, 1000);
      setNeoAnimUno(&neo_animation_alert, left_cal_mode); // top-most leds near the back
      setNeoAnimDuo(&neo_animation_alert, 5+right_cal_mode); // bottom-most leds near the front
      startNeoAnim(&neo_animation_alert);
      
      button_calib_changed = false;
    }

    updateNeoAnimation();
    updateServoAnimation();

  }
  
  updateButtons();

  console();

}


void console() {

  if(Serial.available()) {
    char c = Serial.read();
    switch(c) {
      case '1':
        changeState(STATE1);
      break;
      case '2':
        changeState(STATE2);
      break;
      case '3':
        changeState(STATE3);
      break;
      case '4':
        changeState(STATE4);
      break;
      case '5':
        changeState(STATE5);
      break;
      case '6':
        changeState(STATE6);
      break;
      case '7':
        changeState(STATE7);
      break;
      case '8':
        changeState(STATE8);
      break;

      case 'a':
        decrementState();
      break;
      case 'd':
        incrementState();
      break;

      case 'h':
        Serial << "1-8: states" << endl;
        Serial << "a: r button" << endl;
        Serial << "d: l button" << endl;
        Serial << "h: help" << endl;
      break;
    }
  }

}

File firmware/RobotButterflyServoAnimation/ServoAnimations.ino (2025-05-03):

// ----------------------------------
// ------------ engine --------------
// ----------------------------------

void updateServoAnimation() {
  
  // check if there's an animation happening currently
  // if not, do the home animation
  if(servo_animation_alert.active) {

    if(servo_animation_alert.function) {
      servo_animation_alert.function(&servo_animation_alert);
      updateAllServos();
      //Serial << "left mMillisForCompleteMove: " << wing_left.motor.mMillisForCompleteMove << endl;
    }

  } else {

    if(servo_animation_home.function) {
      servo_animation_home.function(&servo_animation_home);
      updateAllServos();
    }

  }
  
}


bool servoAnimationChecks(struct ServoAnimation *a) {

  if(!a) return false; // safety check

  // check that the animation delay is done. if not, wait again
  if(millis()-a->last_repeat < a->repeat_delay) {
    if(DEBUG_SERVO_ANIM == true && a->type != SERVO_ANIM_HOME) Serial << "animation delay not done" << endl;
    return false;
  }

  // check that the animation duration is complete
  if(millis()-a->start_time >= a->duration  
     && a->start_time != -1
     && a->duration >= 0)
  {
    a->start_time = -1;
    a->repeat_count = 0;
    a->active = false;
    if(DEBUG_SERVO_ANIM == true && a->type != SERVO_ANIM_HOME) Serial << "animation done (time elapsed)" << endl;
    // callback anim done (time elapsed)
    if(onServoAnimDoneCallback) onServoAnimDoneCallback(a);
    return false;
  }

  // check that the number of repeats is complete
  if(a->repeat_count >= a->num_repeats 
     && a->num_repeats != -99) {
    a->start_time = -1;
    a->repeat_count = 0;
    a->active = false;
    if(DEBUG_SERVO_ANIM == true && a->type != SERVO_ANIM_HOME) Serial << "animation done (num repeats)" << endl;
    // callback anim done (num repeats)
    if(onServoAnimDoneCallback) onServoAnimDoneCallback(a);
    return false;
  }

  // increment the frame
  if(millis()-a->last_frame >= a->frame_delay) {
    a->frame_index++;
    if(a->frame_index > a->num_frames-1) {
      a->frame_index = 0;
      a->repeat_count++;
      a->last_repeat = millis();
      if(onServoAnimLoopCallback) onServoAnimLoopCallback(a);
    }
    if(DEBUG_SERVO_ANIM) Serial << "frame (" << a->frame_index << ") " << endl;
  } else {
    return false;
  }

  // if it's here then the animation is active
  // first, reset the vars
  if(a->start_time == -1) {
    a->repeat_count = 0;
    a->frame_index = 0;
    a->start_time = millis();
  }
  a->active = true;
  if(DEBUG_SERVO_ANIM == true && a->type != SERVO_ANIM_HOME) Serial << "Servo animation: " << a->id;
  if(DEBUG_SERVO_ANIM == true && a->type != SERVO_ANIM_HOME) Serial << " frame: " << a->frame_index+1 << "/" << a->num_frames << endl;

  if(wing_left.active == false || wing_right.active == false) {
    if(DEBUG_SERVO_ANIM == true && a->type != SERVO_ANIM_HOME) Serial << "restart servos (" << a->frame_index << ") " << endl;
    if(wing_left.active == false) {
      wing_left.motor.reattach();
      wing_left.active = true;
    }
    if(wing_right.active == false) {
      wing_right.motor.reattach();
      wing_right.active = true;
    }
    a->frame_index--;
    a->frame_delay = 0;
    a->last_frame = millis();
    return false; // fast forward to the next frame
  }

  return true;
}

// ----------------------------------



// ----------------------------------
// ----------- animations -----------
// ----------------------------------

void runServoAnim_none(struct ServoAnimation *a) {

  if(!servoAnimationChecks(a)) return;

  // only 1 frame in this animation
  wing_left.motor.detach();
  wing_left.active = false;
  wing_right.motor.detach();
  wing_right.active = false;
  a->last_frame = millis();

}


void runServoAnim_gentle(struct ServoAnimation *a) {

  if(!servoAnimationChecks(a)) return;

  uint16_t flap_offset = a->helper1;
  uint8_t velocity = a->velocity;

  switch(a->frame_index) {
    case 0: {
      wing_left.motor.setEaseTo( getServoSafeValLeft(SERVO_LEFT_HOME+flap_offset), velocity);
      wing_right.motor.setEaseTo( getServoSafeValRight(SERVO_RIGHT_HOME-flap_offset), velocity);
      synchronizeAllServosAndStartInterrupt(false);
      a->frame_delay = 100+wing_left.motor.mMillisForCompleteMove;
      a->last_frame = millis();
    }
    break;
    case 1: {
      wing_left.motor.setEaseTo( getServoSafeValLeft(SERVO_LEFT_UP), velocity);
      wing_right.motor.setEaseTo( getServoSafeValRight(SERVO_RIGHT_UP), velocity);
      synchronizeAllServosAndStartInterrupt(false);
      a->frame_delay = 250+wing_left.motor.mMillisForCompleteMove;
      a->last_frame = millis();
    }
    break;
  }

}


void runServoAnim_sway(struct ServoAnimation *a) {

  if(!servoAnimationChecks(a)) return;

  uint16_t sway_offset = a->helper1;
  uint8_t velocity = a->velocity;

  switch(a->frame_index) {
    case 0: {
      wing_left.motor.setEaseTo( getServoSafeValLeft(SERVO_LEFT_UP), velocity);
      wing_right.motor.setEaseTo( getServoSafeValRight(SERVO_RIGHT_HOME-sway_offset), velocity);
      synchronizeAllServosAndStartInterrupt(false);
      a->frame_delay = 80+wing_left.motor.mMillisForCompleteMove;
      a->last_frame = millis();
    }
    break;
    case 1: {
      wing_left.motor.setEaseTo( getServoSafeValLeft(SERVO_LEFT_HOME+sway_offset), velocity);
      wing_right.motor.setEaseTo( getServoSafeValRight(SERVO_RIGHT_UP), velocity);
      synchronizeAllServosAndStartInterrupt(false);
      a->frame_delay = 80+wing_left.motor.mMillisForCompleteMove;
      a->last_frame = millis();
    }
    break;
  }

}


void runServoAnim_soaring(struct ServoAnimation *a) {

  if(!servoAnimationChecks(a)) return;

  uint16_t soaring_offset = a->helper1;
  uint8_t velocity = a->velocity;

  switch(a->frame_index) {
    case 0: {
      wing_left.motor.setEaseTo( getServoSafeValLeft(SERVO_LEFT_UP), velocity);
      wing_right.motor.setEaseTo( getServoSafeValRight(SERVO_RIGHT_DOWN-soaring_offset), velocity);
      synchronizeAllServosAndStartInterrupt(false);
      a->frame_delay = 40+wing_left.motor.mMillisForCompleteMove;
      a->last_frame = millis();
    }
    break;
    case 1: {
      wing_left.motor.setEaseTo( getServoSafeValLeft(SERVO_LEFT_DOWN+soaring_offset), velocity);
      wing_right.motor.setEaseTo( getServoSafeValRight(SERVO_RIGHT_UP), velocity);
      synchronizeAllServosAndStartInterrupt(false);
      a->frame_delay = 40+wing_left.motor.mMillisForCompleteMove;
      a->last_frame = millis();
    }
    break;
  }

}
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

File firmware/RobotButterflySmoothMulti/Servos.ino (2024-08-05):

/*
 * Servo Motors
 */ 

void moveLeftWing(uint16_t pos) {

  struct Animation temp;

  // take mutex prior to critical section
  if(xSemaphoreTake(Mutex_SM, (TickType_t)10) == pdTRUE) {
    // critical section
    temp = PresentAnimation;
    // give mutex after critical section
    xSemaphoreGive(Mutex_SM);
  } else {
    if(WARN_SM) Serial << "!! error A1" << endl;
    return;
  }

  struct Animation a;

  a.id = 99;
  a.frames = 1;
  a.start = 0;
  a.active = false;
  a.index = 0;
  a.loop = false;
  a.reverse = false;
  a.done = false;

  a.servo_L[0] = pos; 
  a.servo_R[0] = temp.servo_R[temp.index];
  a.velocity[0] = 50;
  a.dwell[0] = SERVO_MIN_DWELL;

  sendAnimation(&a, ANIM_PLAY);

}

void moveRightWing(uint16_t pos) {
  
  struct Animation temp;

  // take mutex prior to critical section
  if(xSemaphoreTake(Mutex_SM, (TickType_t)10) == pdTRUE) {
    // critical section
    temp = PresentAnimation;
    // give mutex after critical section
    xSemaphoreGive(Mutex_SM);
  } else {
    if(WARN_SM) Serial << "!! error A2" << endl;
    return;
  }

  struct Animation a;

  a.id = 99;
  a.frames = 1;
  a.start = 0;
  a.active = false;
  a.index = 0;
  a.loop = false;
  a.reverse = false;
  a.done = false;

  a.servo_L[0] = temp.servo_L[temp.index]; 
  a.servo_R[0] = pos;
  a.velocity[0] = 50;
  a.dwell[0] = SERVO_MIN_DWELL;

  sendAnimation(&a, ANIM_PLAY);

}

void moveBothWings(uint16_t pos_left, uint16_t pos_right) {
  
  struct Animation a;

  a.id = 99;
  a.frames = 1;
  a.start = 0;
  a.active = false;
  a.index = 0;
  a.loop = false;
  a.reverse = false;
  a.done = false;

  a.servo_L[0] = pos_left; 
  a.servo_R[0] = pos_right;
  a.velocity[0] = 50;
  a.dwell[0] = SERVO_MIN_DWELL;

  sendAnimation(&a, ANIM_PLAY);

}



void initServos() {

  if(!initialised_servos) {
    
    Mutex_SM = xSemaphoreCreateMutex();
    semaphore_anim_frame = xSemaphoreCreateBinary();
    semaphore_anim_loop = xSemaphoreCreateBinary();
    semaphore_anim_done = xSemaphoreCreateBinary();
    semaphore_anim_new = xSemaphoreCreateBinary();

    wing_left.motor = s1;
    wing_left.motor.attach(SERVO_LEFT_PIN, SERVO_LEFT_UP, DEFAULT_MICROSECONDS_FOR_0_DEGREE, DEFAULT_MICROSECONDS_FOR_180_DEGREE);
    wing_left.motor.setEasingType(EASE_QUADRATIC_IN_OUT);
    wing_left.active = true;
    wing_left.name = "LEFT";
    
    wing_right.motor = s2;
    wing_right.motor.attach(SERVO_RIGHT_PIN, SERVO_RIGHT_UP, DEFAULT_MICROSECONDS_FOR_0_DEGREE, DEFAULT_MICROSECONDS_FOR_180_DEGREE);
    wing_right.motor.setEasingType(EASE_QUADRATIC_IN_OUT);
    wing_right.active = true;
    wing_right.name = "RIGHT";

    if(SERVO_LEFT_HOME == -99) {
      Serial << "!! Servo LEFT needs calibration" << endl;
      wing_left.calibrated = false;
    }

    wing_left.home_pos = SERVO_LEFT_HOME;
    wing_left.up_pos = SERVO_LEFT_UP;
    wing_left.down_pos = SERVO_LEFT_DOWN;
    wing_left.current_pos = SERVO_LEFT_UP;
    wing_left.motor.startEaseTo( SERVO_LEFT_UP, 10 );

    if(SERVO_RIGHT_HOME == -99) {
      Serial << "!! Servo RIGHT needs calibration" << endl;
      wing_right.calibrated = false;
    }

    wing_right.home_pos = SERVO_RIGHT_HOME;
    wing_right.up_pos = SERVO_RIGHT_UP;
    wing_right.down_pos = SERVO_RIGHT_DOWN;
    wing_right.motor.startEaseTo( SERVO_RIGHT_UP, 10 );

    initialised_servos = true;
  }

  //disableCore0WDT();
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

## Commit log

2024-02-11 Wizard to guide calibration of servos
2024-02-11 Continuous movement test for servo longevity
2024-03-16 Chonky dev bordzorz1
    [butterfly-chonky.kicad_pcb, butterfly-chonky.kicad_sch, outline.dxf]
2024-04-22 Zweeeop, ZweeeeeeOP, zwoop zwuup
    [butterfly-chonky.kicad_sch, outline-guide.dxf, outline.dxf]
2024-05-14 Yip Yip Yawooooooo
2024-05-30 3d files released to the world
    [assembly_v1.0.step, battery_bracket_v1.0.3mf, battery_bracket_v1.0.stl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]
2024-06-15 Temperature and Humidity
2024-06-29 pesky little sensor
2024-06-30 Added chamfer to underside of lid for nicer printing
    [assembly_v1.0.step, assembly_v1.1.step, lid_v1.0.3mf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]
2024-06-30 Timer stuffs
2024-06-30 Ultrasonic multi task
2024-07-05 update 3d files
    [assembly_v1.1.step, assembly_v1.1_no_colour.step, servo_horn_v1.0.f3d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]
2024-09-03 Hang a robot from a tree with this piece! Cool
    [lanyard_attachment_v1.0.step, lanyard_attachment_v1.0.stl]
2024-09-03 So curious as to why this does not work
    [Buttons.ino, Helpers.ino, RobotButterflyStateMachine.ino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]
2024-12-15 Servo horn bug fix
    [servo_horn_L_v1.0.stl, servo_horn_R_v1.0.stl, servo_horn_flat_L_v1.0.stl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]
2024-12-15 Lanyard attachment increase base height by a few tenths of mm to prevent fasteners from making contact with surface
    [lanyard_attachment_v1.0.stl, lanyard_attachment_v1.1.step, lanyard_attachment_v1.1.stl]
2024-12-15 Assembly update with bug fix for spacer back
    [assembly_v1.1.step, assembly_v1.2.step]
2024-12-15 Spacer Back bug fix
    [spacer_back_v1.0.stl, spacer_back_v1.1.stl]
2024-12-18 Tricky buttons
2024-12-20 Another go at buttons
2024-12-20 Double click button try
2024-12-20 Better buttons
2024-12-20 Buttons complete
2024-12-21 Buttons in FreeRTOS task
2025-02-20 The reason why gitignore did not work was because git pull was not done locally before adding the files. Sigh Lol
    [Helpers.ino, RobotButterflyManufacturing.ino]
2025-02-20 Add info about the LEDs from the instructions
2025-02-24 IMU basic
2025-02-25 IMU work in progress
2025-02-25 IMU WIP
2025-02-27 IMU refactoring and organising
2025-02-27 IMU orientation detection
2025-02-27 IMU event detection
2025-03-03 Print IMU stats and some fine tuning
2025-03-03 IMU callbacks added
2025-03-03 IMU RTOS Task
2025-03-17 Organised LED colours
2025-03-17 Tidy up, refactor, fix an off-by-one error
    [NeoAnimations.ino, NeoColours.ino, RobotButterflyNeoAnimation.ino]
2025-03-17 Squiggle animation bug fixes
    [NeoAnimations.ino, RobotButterflyNeoAnimation.ino]
2025-03-20 imu api and tidy up
2025-03-20 new servo animations
2025-03-21 flutter servo animation
2025-03-21 Jingles musical buzzer sounds yay
    [Helpers.ino, RobotButterflyBuzzer.ino]
2025-03-22 sensors work in progress
2025-03-23 sensor struct, atomic wip
2025-03-24 timer fixes and sensor progress
    [RobotButterflySensors.ino, Sensor.ino]
2025-03-24 sensor update function improvements
2025-03-24 sensor cleanup and ambient improvements
2025-03-24 temperature sensor work in progress
2025-03-25 fix up the interrupt and add in additional sensors for long test
    [RobotButterflySensors.ino, Sensor.ino, Sensor_Battery.ino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]
2025-03-26 prior to switching dht11 libraries
2025-03-27 Sensor improvements
2025-03-27 DHT11 sensor read toggle
2025-03-27 Happy five sensors
2025-03-28 archive old ultrasonic version
2025-03-28 new ultrasonic version
2025-03-28 proximity moving average filter
2025-03-28 archive old servo movements
2025-04-07 servo anim api cleaning
2025-04-08 imu timer update
2025-04-08 Sound buzzer control update
    [RobotButterflySound.ino, Sound.ino]
2025-04-08 Button modifications
2025-04-21 bettery battery
2025-04-21 bettery battery integrated
2025-04-21 calibration mode
2025-04-30 function pointers for buttons
2025-04-30 imu function pointers
2025-04-30 sensor function pointers
2025-04-30 servo animation function pointers
2025-05-03 mini tidy up servo anims
2025-05-03 servo animation module
2025-05-03 minor sensor tweaks
2025-05-03 library sensor module
2025-05-04 buttons rtos sandbox sketch
2025-05-17 state machine timer bug fix
2025-06-04 Organised schematic
    [butterfly-chonky.kicad_sch]
2025-08-24 minor tweak to have leds on

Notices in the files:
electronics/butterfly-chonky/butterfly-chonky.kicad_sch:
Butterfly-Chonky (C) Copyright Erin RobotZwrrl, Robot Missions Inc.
